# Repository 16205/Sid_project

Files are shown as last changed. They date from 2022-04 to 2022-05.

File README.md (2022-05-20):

# **SID Project**

#### A Robotic project - Stereo Imaging Device  
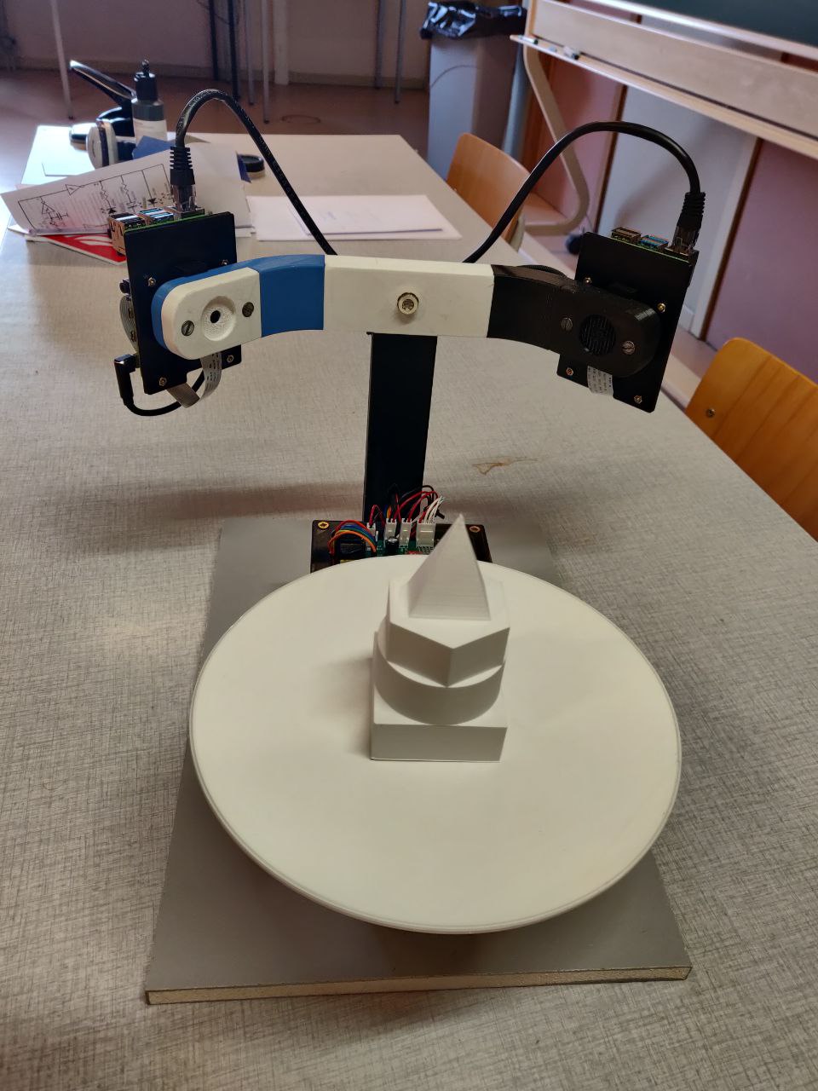
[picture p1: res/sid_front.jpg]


## Project participants  

- Nicolas SAMELSON 17288
- Raphaël JADIN 21295
- Gabriel LOHEST 16205

## Introduction

The goal of this project was to design a 3D scanner, develop an interface and scripts to output the scanned object into a 3D STL file, ready to import into a 3D CAD design software.  

This project is still in a phase of a prototype and therefore not a finnished product.  
All the files for the interface, the script, the PCB and the 3D CAD designs were developped in an "Open-Box" extensibility model. The ```main``` branch contains the code, the ```pcb``` branch contains the PCB design files and the ```3D-printed-hardware-CAD``` branch contains the models to print.  

## 1. Material used

- 2 Raspberry pi 4
- 2 Raspberry pi camera (module V2.1)
- 1 Stepper motor (Nema 17 10:1)
- 1 driver (A4988)
- 1 Power supply AC/DC 5V and 12V
- 1 display 11"
- 1 red line laser (HLM1230)

## 2. Interface (Kivy)

The interface files are stored inside the folder [/code/screen/](https://github.com/16205/Sid_project/tree/main/code/screens). 
Inside, there are 4 files, each for a specific screen interface.  

### 2.1. HomePageScreen
This corresponds to the home page of the interface. The user is presented with 4 buttons : 
- **Run**, to access the ```RunScreen```;
- **Settings**, to access the ```SettingsScreen```;
- **Storage**, to access the ```StorageScreen```;
- **Exit**, to exit the application.

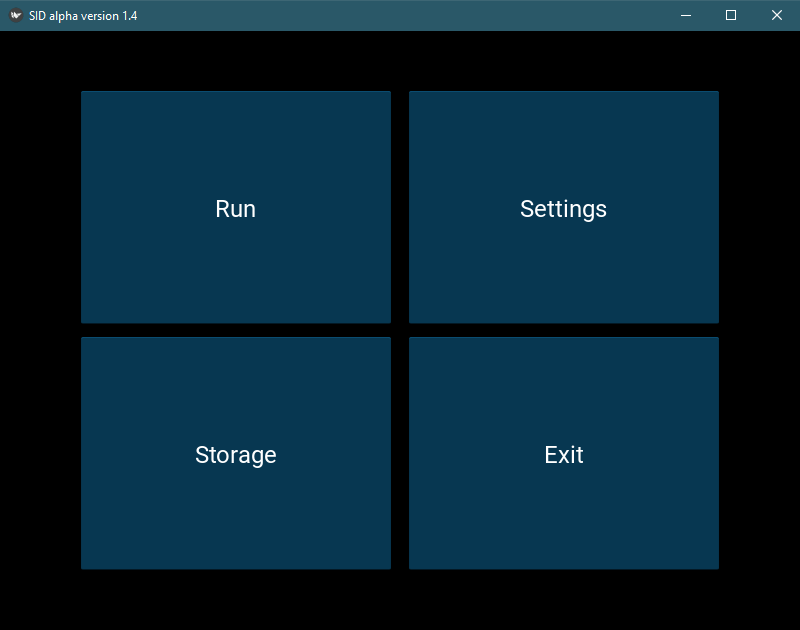
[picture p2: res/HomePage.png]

### 2.2. RunScreen
This interface contains all the quick parameters to set before a scan and the button to start a scan :
- **Resolution** is used to set the number of pictures taken;
- **Scale** is used to set the size of the object to scan;
- **Laser power** is used to adjust the intensity of the laser;
- **The set of 3 radio buttons** helps visualize the pictures taken in different color spaces.

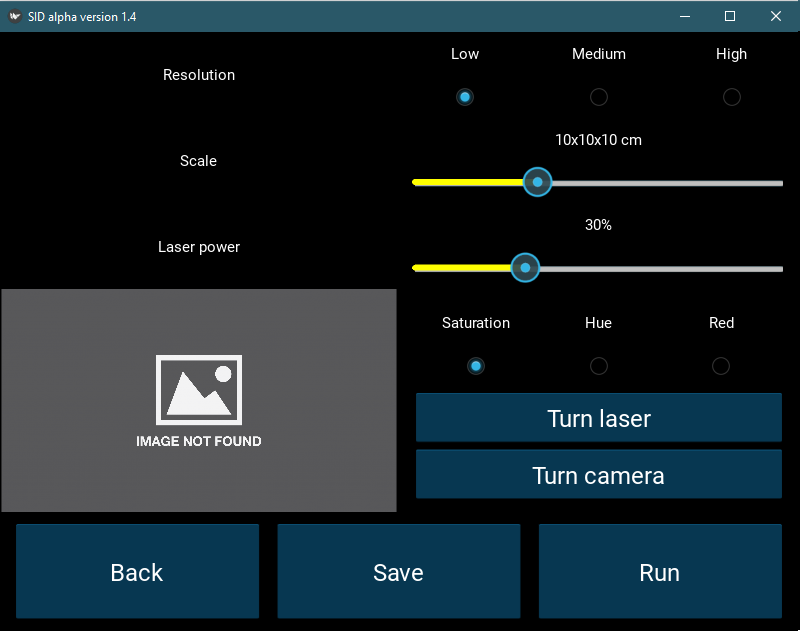
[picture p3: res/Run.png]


### 2.3. Settings
This interface is used to setup the calibration needed to scan (only the first time the application is launched) :
- **Connect** helps setting up the video stream of the slave raspberry pi camera;
- **Slave(L)** and **Master(R)** are used to have a video feedback of the 2 cameras;
- **Capture/Calibrate** launches the script of ```calibration```.

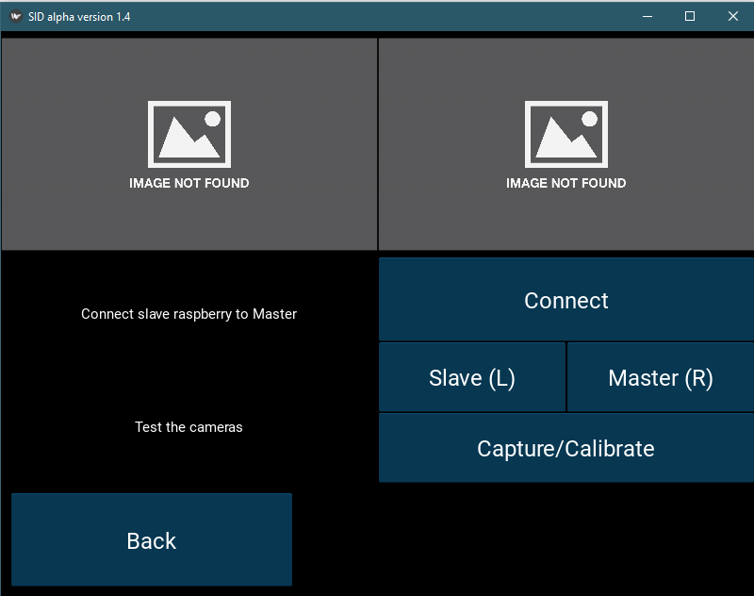
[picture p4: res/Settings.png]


### 2.4. Storage
The storage interface helps the user to manage its scans, as well as convert it in a 3D STL file.

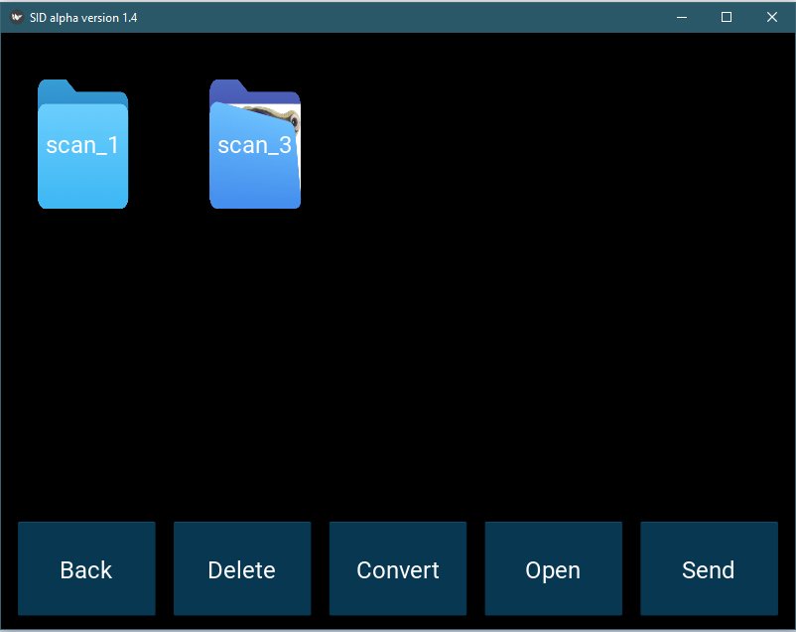
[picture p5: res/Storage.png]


## 3. Scripts

### 3.1. Main.py

Run the script [main.py](https://github.com/16205/Sid_project/blob/main/code/main.py) to launch the interface

### 3.2. On the Raspberry pi Master

#### 3.2.1. Different Files
In the [/code/raspberry/](https://github.com/16205/Sid_project/tree/main/code/raspberry) folder, you can find the following scripts :
- ```GPIO_setup.py``` : used to set the correct pins in read/write at the start of the application;
- ```copy_slave_pics.py``` : after a scan , the master will copy the pictures taken by the slave in its own folder;
- ```laser.py``` : used to turn on/off and adjust the intensity of the laser;
- ```prise_image_bon.py``` : takes a picture from the master and writes it into a folder with the name of the scan;
- ```scan.py``` : main script that manages the scan (turns the laser, takes pictures, turn the stepper and copy the slave pics);
- ```sshTools.py``` : used to run commands from the master to the slave via the SSH protocol;
- ```stepper.py``` : used to command the stepper and turn a determinated number of steps;
- ```stream.py``` : used to command the slave to stream its video feed through rtsp.

#### 3.2.2. Stereovision Folder
The stereovision folder contains the scripts to calibrate the cameras, but also to transform the pictures in a cloud of 3D points : 
- ```calibration.py```: calibrates the cameras;
- ```prepross.py```: generate a new binarized image with in white the laser and the rest in black
- ```image_processing.py```: contain the stereovision methods 
- ```scan_processing.py```: run the stereovision methods on a scan and then generate a JSON file with the world coordinates in the opencv calibration referential.
- ```post_processing.py```: achieve the revolution of all the laser lines and save the point cloud to a json.
- ```jsonTools.py```: Library to create json files and get data from json files
- ```mathTools.ty```: Library with mathematical functions for the image processing

#### 3.2.3. Post-processing Folder
This folder contains the scritps to transform a cloud of points into a 3D STL file : 
- ```create_stl.py``` : takes in input a json file in a 3 dimensions matrix and outputs a STL file;
- ```create_points.py``` : creates json files to get examples of working models.

### 3.3. On the Raspberry pi Slave
- ```prise_image_bon.py```: take picture and save it into the asked folder. Runned from the master in ssh.

## 4. PCB design
The [pcb](https://github.com/16205/Sid_project/tree/pcb) branch contains the Gerber files to print through JLCPCB.  
You can find the scematics and the design in the [pdf](https://github.com/16205/Sid_project/tree/pcb/pdf) folder.

The point of this PCB is to have one board, connecting all the needed cables as well as having easy access to the pins. It contains a footprint for :
- A A4988 driver;
- 2 USB-A 2.0 female ports;
- 1 capacitor (12V)
- 1 potentiometer
- pins for the stepper, the alimentation (5 and 12V), the laser and the raspberry pi (master)

## 5. Continue the project

Please Fork the repository if you want to continue our project. If you just want to test it, just clone it.

### 5.1. Dependencies

The project needs you to have a python version of ```3.8.10``` or older, with the following pip modules installed : 
- ```numpy```
- ```numpy-stl```
- ```opencv-python```
- ```mathutils```
- ```kivy```
- ```RpiMotorlib```

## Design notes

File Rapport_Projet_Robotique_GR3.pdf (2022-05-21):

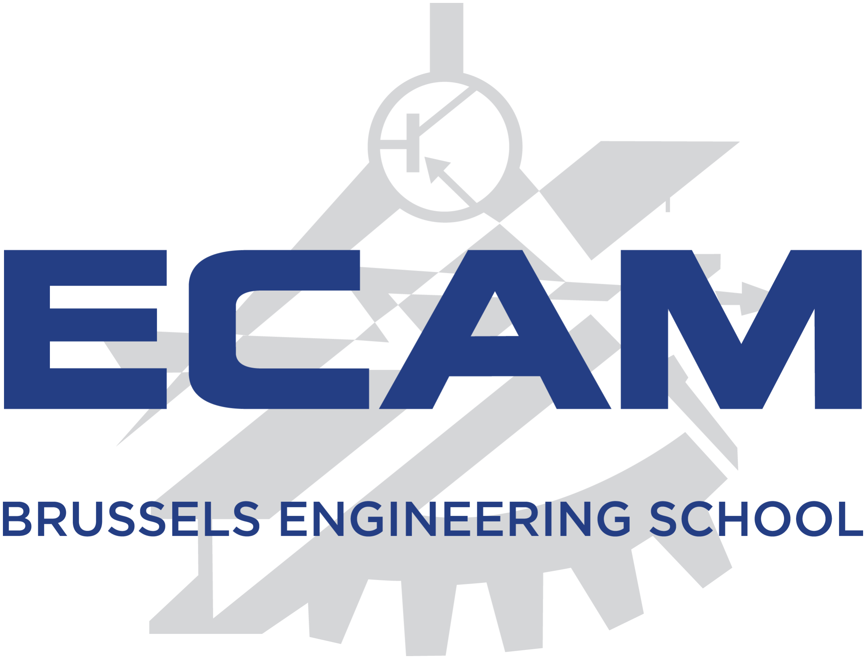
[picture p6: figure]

ECAM Brussels Engineering School

2021-2022

# Robotic Project:

## Stereo Imaging Device

Rapha¨el | JADIN | 21295
Gabriel | LOHEST | 16205
Nicolas | SAMELSON | 17288

May 21, 2022

## Contents

1 Introduction | 1
2 Materials and technologies | 2
2.2.3 | Image pre-processing, stereovision and point cloud post-processing . | 8
3 Project timeline | 13
4 Demonstration | 15
5 Critics & alternatives | 16
6 Conclusion | 20
References | 23

## List of Figures

1 | PCB design | | 2
2 | PCB schematic | | 4
3 | Slide rail mounting system separate design & testing | | 5
4 | Camera & laser housing, with Raspberry Pi supports | | 5
5 | Motor mount & rotating table | | 6
6 | Power supply case & vertical linking element | | 6
7 | Final assembly | | 7
8 | Image taken from the slave (Left) and image taken from the master (Right) | 9
9 | Generated binary pictures | | | 9
10 | Epipolar geometry | | 10
11 | Example of mesh | | 11
12 | Top view of a cylinder | | 12
13 | SID photo | | 15
14 | 3D mesh of the scanned piece | | 15
15 | Schema of the application with one laser and one camera | | 19

## 1 Introduction

The first 3D laser scanning device was developed in the 1960s, and consisted of lights, cameras and projectors. Due to the limitations of the equipment at that period, the scans took a lot of time and effort to be roughly accurate. It’s only in the end of the 20th century, with the democratisation of computers that the technology took a big leap forward. The methodology carried on improving, by making a scan more accurate, faster, truly three dimensional, and able to distinguish surfaces by color.
Later, with the democratization of 3D printing devices in 2005, the 3D laser scanning market grew even further.

During the Robotic Project course, we focused on creating a 3D scanner device, with the technologies of a laser and 2 cameras. Our objective was to make it open-source, affordable and modular, allowing a large range of compatibility with components.

The scanner is able to scan objects of a maximum size of 14cm in diameter and 15cm in height. The object is placed on a rotating plate, which is controlled by one of the two Raspberry Pi 4. After a scan, the device will transform the images taken in a 3D point cloud through stereovision technology. Finally, the user will be able to export a 3D file (in STL format) which could be imported into a 3D CAD software.

1

## 2 Materials and technologies

### 2.1 Hardware

Below is a list of the components used in this project. As mentioned earlier, the project is open-source and the design is modular. This means that the components could easily replaced by other ones.

List of components :

- 1x 11-inch LCD touchscreen
- 2x Raspberry Pi 4
- 1x 5 mW stripe laser
- 2x Pi Camera v2
- 1x NEMA 17HS15 stepper motor
- 1x A4988 Driver
- 1x AC/DC 5V and 12V power supply
- 1x Custom designed PCB
- 1x Custom 3D-printed assembly
- 2x USB-A to USB-C cables
- Multiple breadboard jumper wires

### 2.1.1 PCB & wiring

A PCB has been designed to handle all connections between the 2 Raspberry Pis, the stepper motor, the laser and the power supply. It was sketched with the help of the software EasyEDA.

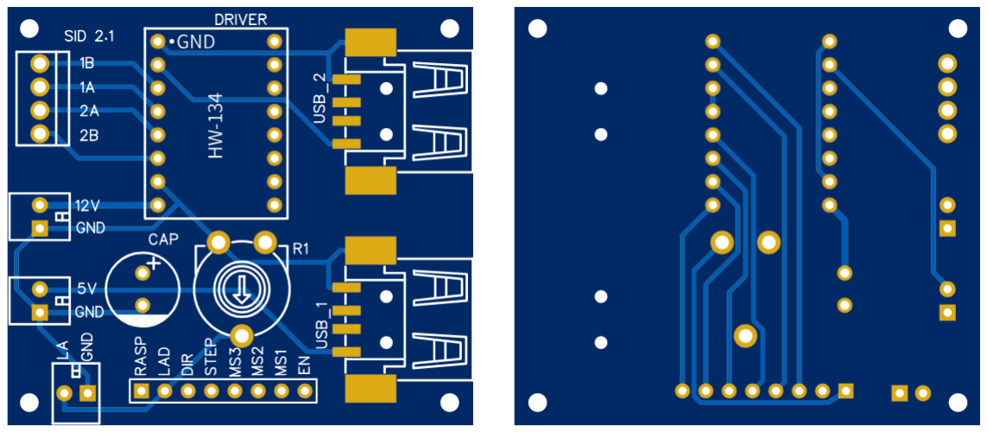
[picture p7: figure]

Figure 1: PCB design

2

On the PCB design at Figure 1, we can find footprints for the A4988 driver, 2 female USB-A ports, a potentiometer, a capacitor, and 5 blocks of connectors :

- 2x 2-pin connectors, used to connect the power supply outputs (5V and 12V)
- 1x 4-pin connector, to plug in the stepper motor
- 1x 2-pin connector, to plug in the laser
- 1x 8-pin connector, to link the Raspberry Pi and control the components.

First, the power supply brings 12V and 5V on the PCB. The 12V is used to power the stepper motor, which accepts a voltage between 9V and 35V. The 12V tracks, which are 0.69mm thick, pass through the driver. A 100 µF capacitor is also connected in parallel to the 12V source (see Figure 2).
The 5V tracks, which are 0.49mm thick, power the driver itself as well as the rest of the components.

The 2 USB ports are used to power each Raspberry Pi through a USB-A to USB-C cable. On the schematic (Figure 2), the USB connectors we used have the GND and VCC pins inverted (the component in red) between the schematic and the actual footprint, and therefore precaution is needed to avoid a short-circuit.

The 8-pin connector is used to control all components with the Raspberry Pi.
The 2 first pins (RASP and LAD) are used to power the laser. LAD connects it directly to the laser connector while RASP is connected in series with a potentiometer. This was originally intended to help the user control the intensity of the laser (with a knob on the potentiometer) in case the control through software wouldn’t be reliable (the Raspberry Pi needs to use its Pulse Width Modulation).

The 6 other pins are used to control the stepper motor. The DIR and STEP pins are used to control the direction of the rotation and the instruction to make a step, while MS1, MS2 and MS3 determine what the step size should be (the Nema 17HS15 is able to go down to a 16th of a step thanks to its gearbox [ref. 24].
Finally, the EN pin enables or disables the stepper.

3

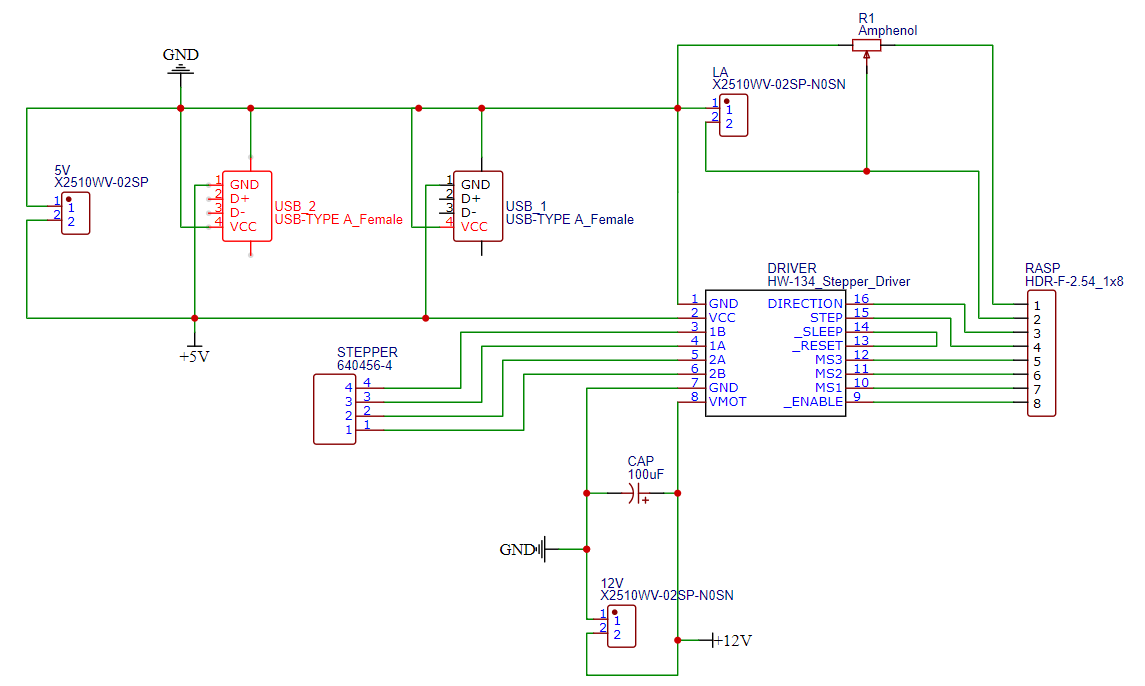
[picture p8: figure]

Figure 2: PCB schematic

4

2.1.2 3D Design & printing

The main body of the project is made of several 3D-printed parts, that have all been designed with Dassault Systemes’s SOLIDWORKS software. The initial goal was to be able to integrate all components in a single piece of hardware, so that the project could hold itself together as a whole. This has been achieved, thanks to a modular approach, resulting in a number of individual parts.

A slide rail mounting system has been conceived and separately tested before being integrated to most parts. This solution was chosen in order to make it easier to iterate design changes, to avoid having to print out the whole thing again at every new version. It also happened to be convenient because the 3D printer had a limited footprint. The slide rail mount also eliminated the need for fasteners, like screws and bolts, or even glue, thus making the final assembly an easier process.

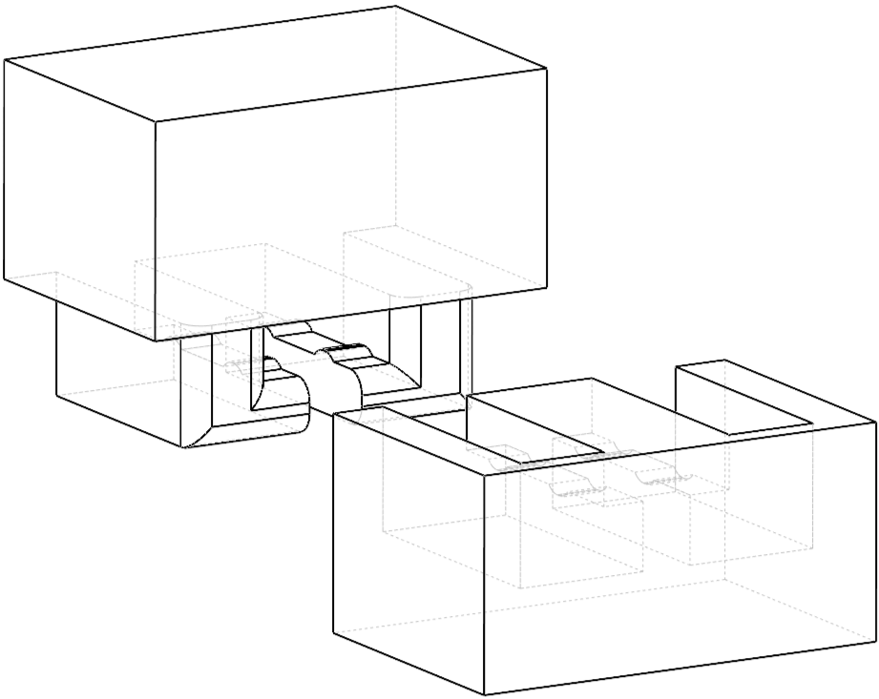
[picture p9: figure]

Figure 3: Slide rail mounting system separate design & testing

The assembly is essentially composed of 3 main parts, which are themselves made of subparts. The camera and laser housings, with the supports holding the raspberries in place. This is a nearly symmetrical part, except for a few details.

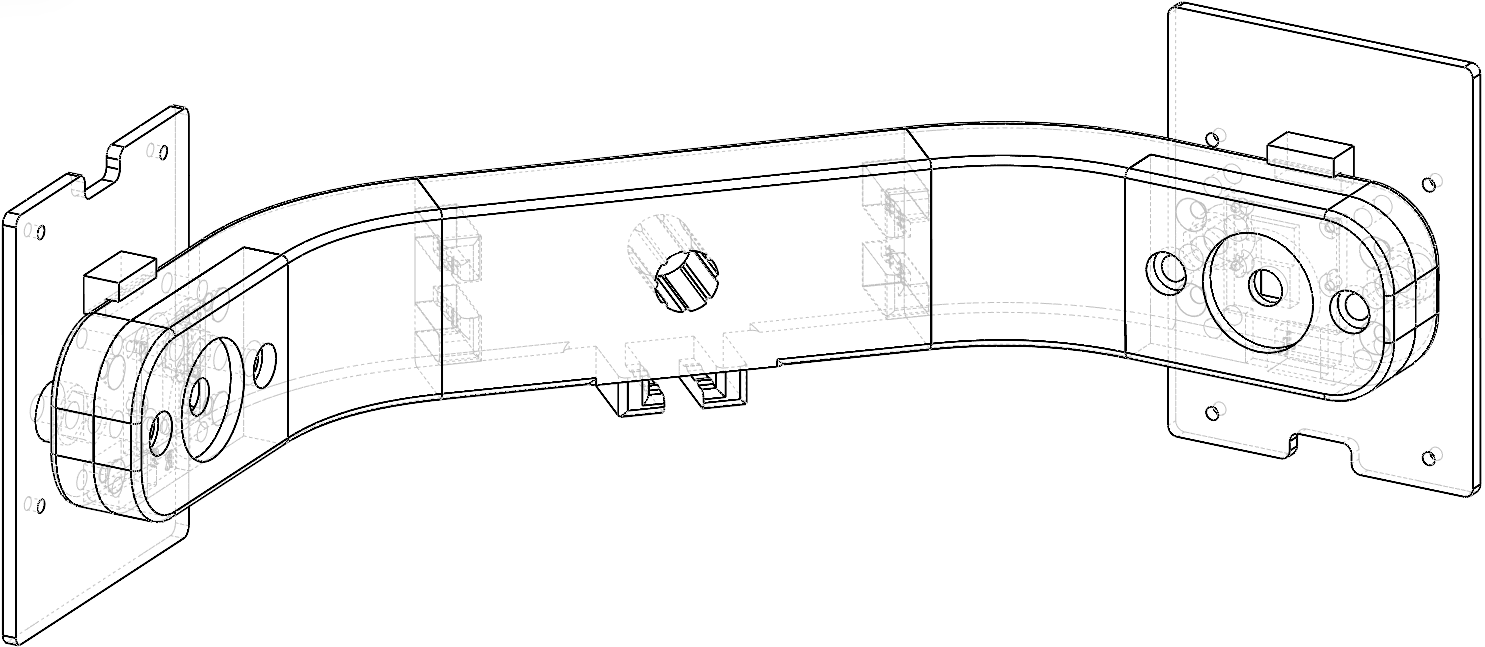
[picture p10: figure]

Figure 4: Camera & laser housing, with Raspberry Pi supports

5

Then, we have a motor mount for the Nema stepper motor, and a rotating table, lying on an appropriate thrust roller bearing, serving as mechanical coupling between the two.

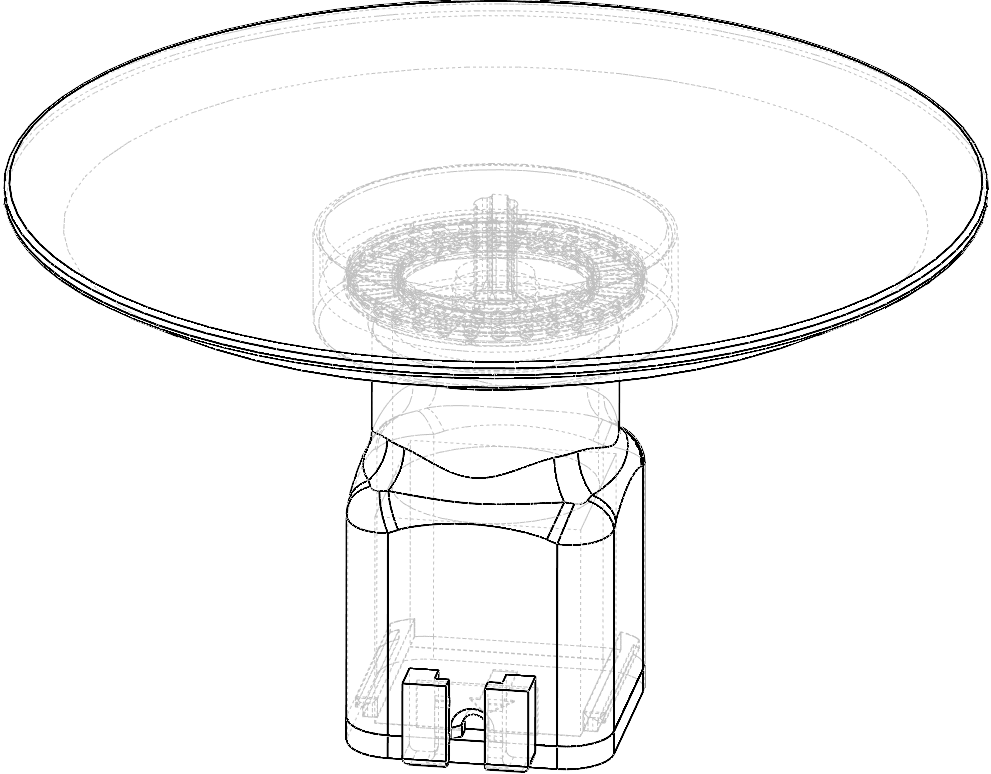
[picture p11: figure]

Figure 5: Motor mount & rotating table

Finally, the power supply case holds all the wires, the PCB, as well as the power supply unit. The vertical link part that connects to the camera and laser housing has a groove serving as a guide for the wires.

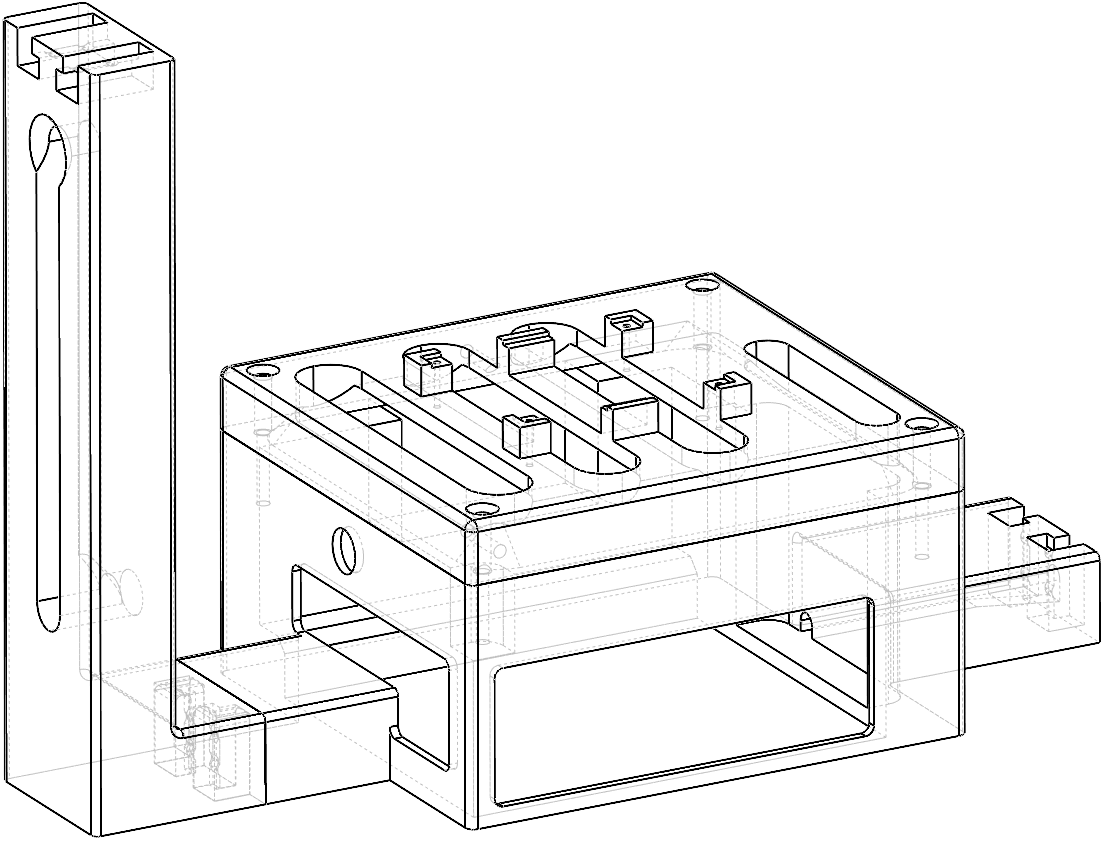
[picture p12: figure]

Figure 6: Power supply case & vertical linking element

6

The final assembly looks like this:

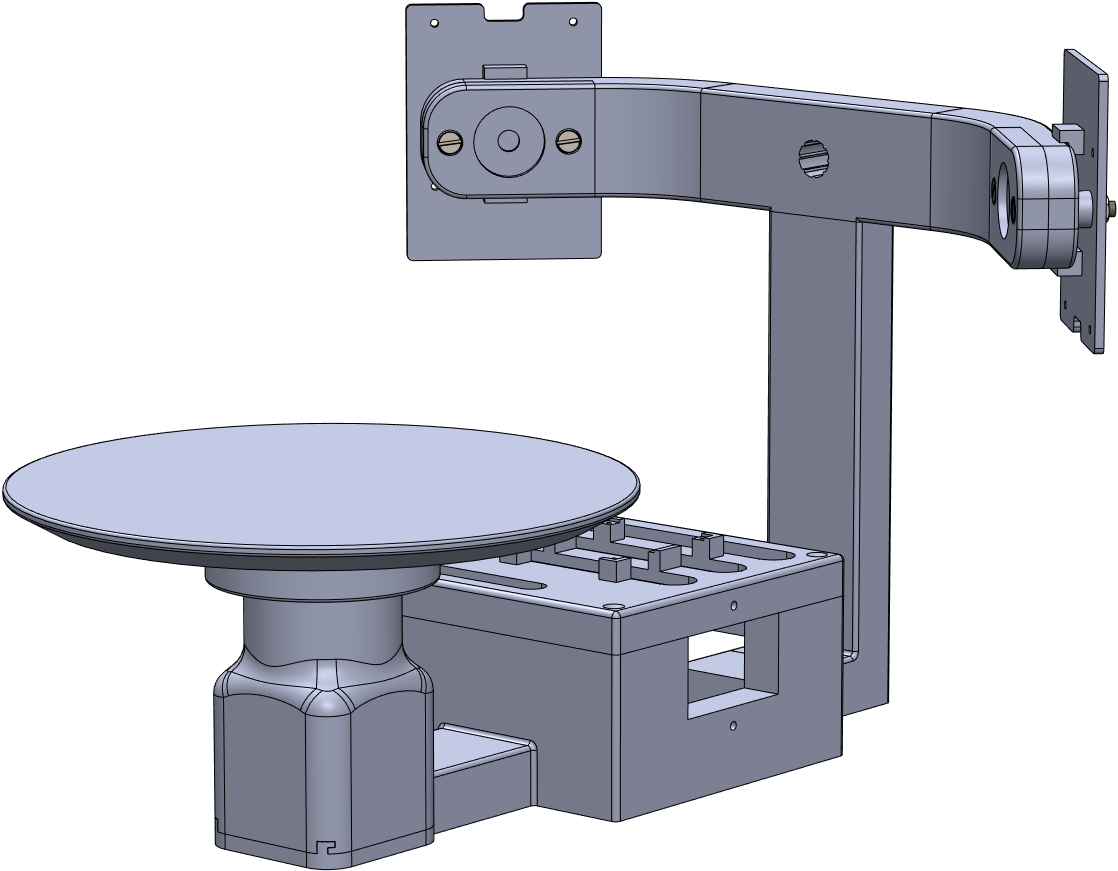
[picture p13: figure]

Figure 7: Final assembly

The choice was made not to integrate the touchscreen into the assembly. This is because of its bulky dimensions, but mainly because there were doubts during the development of the project as to whether it was needed or not. However, it ended up being part of the prototype, and can easily be connected and put in position right next to the project assembly, thanks to its integrated folding leg.
All files concerning the 3D CAD are available on GitHub [ref. 22].

### 2.2 Software

### 2.2.1 User Interface

For the user to be able to interact with the scanner, we have connected a 11-inch touchscreen to the Raspberry Pi master. In order to create the UI, we used the Kivy framework (based on python) as it offers cross-platform ability, an easy interaction and works well with touchscreens.

The UI is used to start the connection between the 2 Raspberry Pi’s together, calibrate the cameras, launch a scan, and convert the scan into a usable 3D file (STL format). A complete description of each page and their functionalities can be found on GitHub [ref. 21].

7

### 2.2.2 Communication protocols

Because we are using a second Raspberry pi (to connect the second camera), we used multiple communication protocols in order to take pictures on the slave and also to copy files from the slave to the master.

NFS

NFS, or Network File System, is a protocol that allows a client computer to mount a remote computer’s disk to its own file system, in order to access the remote files over the network. In our case, we implemented it to share the home folder of the slave Raspberry Pi over the master Pi. The network connection between both computers is secured by an Ethernet cable.
By accessing the files of the slave Pi via NFS, we can retrieve the images taken during the scan, and considerably faster than over another protocol, like for example, SSH.

SSH

The SSH protocol is widely used to remotely access the terminal of another machine. In our specific case, we used it to send commands to the slave Pi, for it to capture an image when needed.
The goal here is to run the script prise_image.py, which is stored on the slave Pi. This script, when run, triggers the capture of a picture with the slave Pi’s camera, and then stores that picture on the slave Pi’s own file system. One tricky part was to use SSH from a script on the master Pi, instead of directly from the terminal. In order to achieve this, we used the pexpect [ref. 18] and pxssh [ref. 20] libraries. Another difficulty arose, concerning the robustness; we need to make sure the slave Pi’s image has been captured, before the stepper makes the next step. To solve this problem, we used the NFS to check whether the image was successfully taken. If so, the stepper was then instructed to do the next step; if not, the image-taking script was re-run on the slave.

RTSP

RTSP, or Real-Time Streaming Protocol, is a network protocol designed to transport information streams, such as a video live-stream, over a transport protocol (i.e. UDP [ref. 31] or TCP [ref. 29] ).
In our case, it is used for the cameras’ calibration. The calibration script launches the stream on the slave, through SSH. The master is then able to access it and take video captures.

### 2.2.3 Image pre-processing, stereovision and point cloud post-processing

This part is composed of three main steps. First, we need to get the image coordinates (i.e. the x and y position relative to the upper left corner on the image) of the pixels which represent the laser projection. Then, based on those points, the stereovision technology is used to get the world coordinates of the points (i.e. the coordinates in a referential given by the OpenCV calibration). Finally, we need to process all the points in such a way that allows to model the scanned object.

8

Image pre-processing

This is the part where the images taken by the camera are processed in order to isolate the geometry of the laser projection on the object. A binary image¹
is then generated:
the pixels are black everywhere, except where the laser projection was detected, where the pixels are white.
To this purpose, the OpenCV library was used. This is an open source library developed by Intel, dedicated to image processing. It can be used in C++ or in Python, the latter of which is our case.

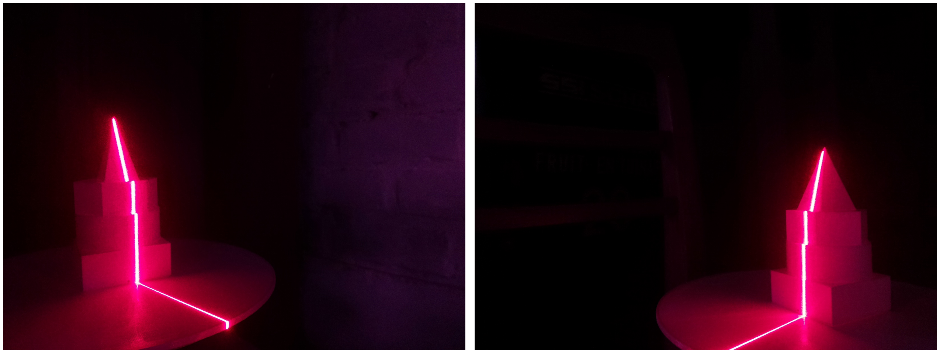
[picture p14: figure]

Figure 8: Image taken from the slave (Left) and image taken from the master (Right)

On the images at Figure 8, one can observe that the center of the laser line appears to be white. This is due to the intensity of the laser, that saturates the sensors of the cameras. In order to isolate the desired pixels, we took advantage of this. The threshold function of OpenCV was used on all three channels of the image (blue, green and red). This allows to generate these binary images, containing the laser line.

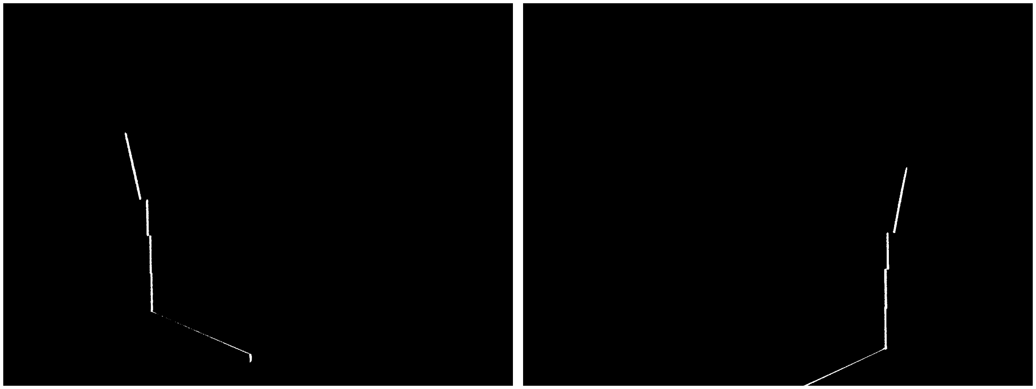
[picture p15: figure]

Figure 9: Generated binary pictures

Thanks to these cleaned up images, the actual stereovision processing can now start!

1A binary image is an image where the pixels have two possibles values: 0 for black and 255 for white

9

Stereovision

The following explanation is about one single left and right image pair at a time, but the process is obviously looped in such a way that all image pairs of a scan are processed in this way.
The first step is to narrow the laser line’s width down to a single pixel, on the binary image from the left camera, by taking the average coordinates of that width. These coordinates are then stored in the following format: (x = average x, y = line number, z = 1).

The next step is to find the corresponding pixels on the binary image from the right camera. This is done thanks to the epipolar geometry [ref. 7].

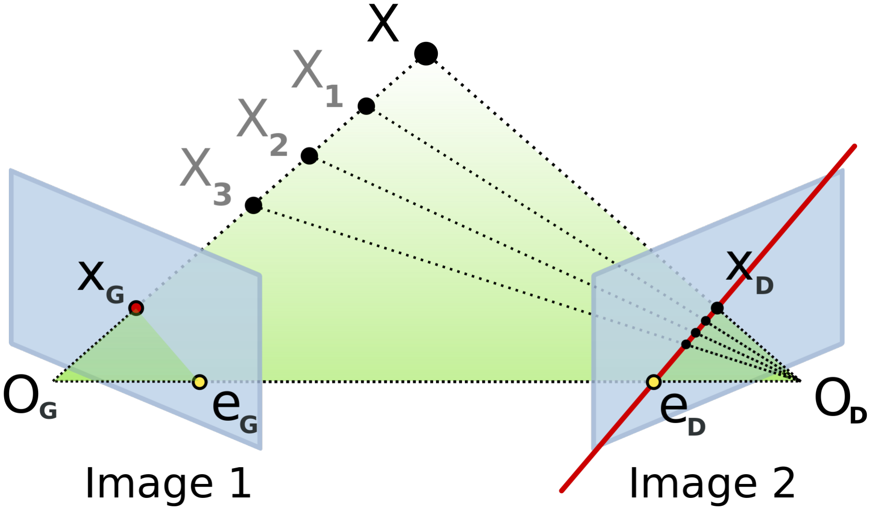
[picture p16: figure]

Figure 10: Epipolar geometry

Then, matching the pixels from the left and right images (i.e. XG on the left image and XD on the right image, in Figure 10) makes it possible to find the intersection of the [Og, XG] and [OD, XD] lines, on Figure 10. The coordinates of that intersection are in fact the previously mentioned ”world coordinates” of the laser line.
As every pair of left and right images corresponds to a step of the motor, all the world coordinates from a pair of images are stored in a JSON file, and referenced as follows :

{stepn : [[Y1, Y1, Z1, 1], [X2, Y2, Z2, 1], ..., [Xp, Yp, Zp, 1]], stepn+1 : ...}

each point having coordinates in the homogeneous [x, y, z, 1] form.

At this point, the current coordinates do not yet permit the reconstitution of the scanned part. To make this possible, we need to integrate the concept of rotation in order to stitch together all the data from every individual image pair, to be able to create the point cloud model. This is done in four steps :

1. Apply a transformation to move the origin of the coordinate system given by the OpenCV calibration (”world coordinates”), to the center of the table of the scanner.
2. For each step of the motor, and thus each image pair, a rotation has to be applied. The rotation angle for each image pair, or step n, can be computed as follows:

α = step angle ∗ stepn

where step angle is the angle covered by a step.

10

3. Find the ratio between a distance unit in the virtual referential and a millimeter in the real world.
4. Convert the homogeneous coordinates to ”real-world coordinates” in a referential with the same origin but where a unit is one millimeter.

Once all these steps are done, every ”real-world point” has to be written in a JSON file in the same way than previously explained. This JSON file then contains what we call the point cloud model of the object. The coordinates are organized in such a way that every column is the set of points from a step, i.e. a pair of pictures. This formatting is well suited for the point cloud post-processing.

### 2.2.4 Point cloud post-processing

The script create_stl.py takes care of the transformation of the point cloud into an exploitable STL file. When run, the script first retrieves the point cloud JSON file, and transforms it in a 3-dimensional array of points. The first dimension is the column (each column representing a step in our scan), the second is the row (or the points) and the last dimension contains the x, y and z coordinates of each point.

[
[[1.0, 0.0, 0], [1.0, 0.0, 1], [1.0, 0.0, 2]],
[[-1.0, 0, 0], | [-1.0, 0, 1], | [-1.0, 0, 2]]
]

In the example above, we have a 3D array of 2 columns and 3 points for each column. The 3D array is constructed with the help of the numpy library, allowing fast manipulations of arrays.

Before turning the 3D array into a STL file, each column of the point cloud needs to have the exact same amount of rows (or points). This is because a 3D mesh is constructed of triangles (see Figure 11). In our case, 2 triangles are formed from 2 points of 2 consecutive columns. For example on Figure 11, the triangle a and b are based on four points (2 are in common).

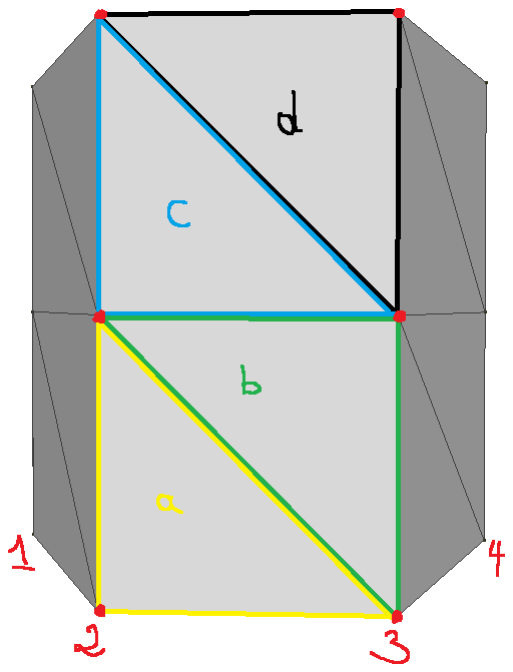
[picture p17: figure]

Figure 11: Example of mesh

11

In order for all columns to have the same amount of points, the array has to be processed by an algorithm that adds missing points where it is needed. We set the reference column as the one with the biggest number of points in it, in order to keep maximum resolution.

This algorithm first checks the endpoints of each column and compares it with its neighboring columns (e.g. we study the column number 2 on Figure 11, its neighbors are the column 1 and 3). As the first item in the column is the point with the lowest z coordinate and the last the highest z coordinate, we can compare those heights with with the endpoints of the neighbors columns. If the difference in height between the studied endpoints (bottom and top of column 2) and its neighbor endpoints (column 1 and 3) are greater than 10%, it fills in a new point at the mean height of its 2 neighbors.

The second part of the algorithm adds missing points between the 2 ends. This is done by calculating the average step the studied column should have, with the following formula :

step = lowest +

highest − lowest + 1
max rows
where
- lowest is the first item of the column, which has the lowest z coordinate,
- highest is the last item of the column, having the highest z coordinate,
- max rows corresponds to the number of points the reference column has.

For a given step, we can iterate through its column and add missing points if the difference between the step and the next point’s z coordinate is greater than 10%. After repeating this for each column of the array, they should now all have the same number of points.

We can now transform the 3D array into a 2D array of vertices and faces. The vertices correspond to our points in the 3D array that is flattened into a 2D array [ref. 15].
The faces are an array of the triangles we construct. A single triangle needs 3 points, and for the mesh to show the face in the correct direction, we need to order the 3 points as to draw it clock-wise (if we were to join the 3 points together).

Now all the points (vertices) are linked to triangles. But the top and bottom of the object are still not connected. To solve this problem, we can simply add a point in the middle at the top of the piece (see Figure 12) and draw triangles between the center and 2 points at the top of their respective column. The same was done for the bottom.
Finally, with the help of the numpy-STL library, we can create a 3D mesh and save it in STL format.

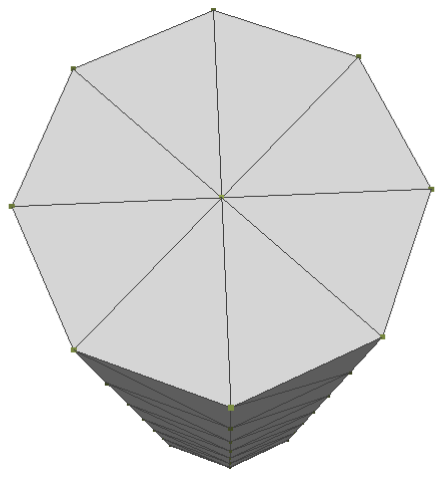
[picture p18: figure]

Figure 12: Top view of a cylinder

12

## 3 Project timeline

### 3.1 Sprint 1

- design a PCB for the driver;
- first version of 3D design for laser and camera support;
- establish the connection between the slave Pi and the master Pi;
- validate and command the pcb;
- taking images from both rapsberry pi and transfert the images from slave Pi to master Pi;

### 3.2 Sprint 2

- first verion of the U.I.;
- design the box for the stepper motor and the scanner’s table;
- print the box for the stepper motor;
- calibrate the cameras;
- import the U.I. on the master PI;
- test and weld the components on the pcb;
- finalize the U.I.;

### 3.3 Sprint 3

- make the stepper operational;
- insert the code of the stepper into the U.I.;
- 3D design : attached the slide rail;
- insert the scripts for the scan in the U.I.;
- finalize the pcb and the wiring;
- new supports for the camera and the stepper motor.

### 3.4 Sprint 4

- achieve a scan of an object and get pictures from the slave;
- extract the pixels of the laser and get their world coordinates;
- make a json with the coordinates of the extracted points from the scan and format it properly;
- all the 3D pieces are printed and fits together;

13

- image processing code refactored to make it more extensible;
- create an stl file from a point cloud
- cable management is done properly;
- camera calibration is runable from the interface.

14

## 4 Demonstration

A piece was placed on the center of the table (see Figure 13). We launched a scan which took a 100 photos (for each camera). Here is the result of the 3D mesh in a STL format at Figure 14.

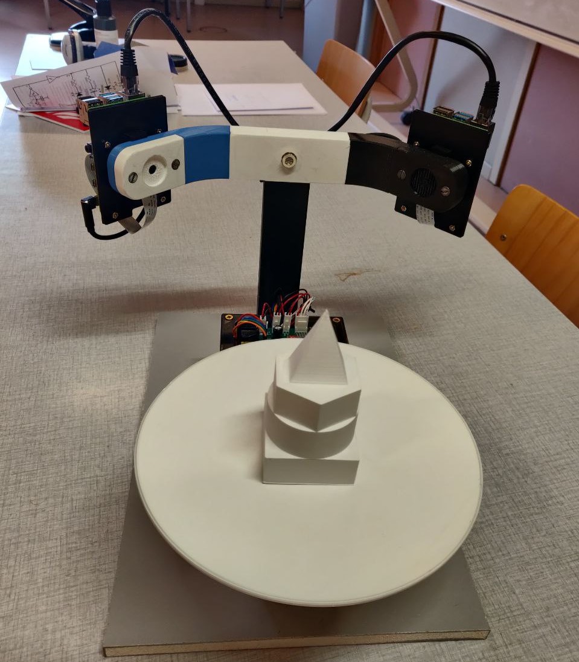
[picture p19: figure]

Figure 13: SID photo

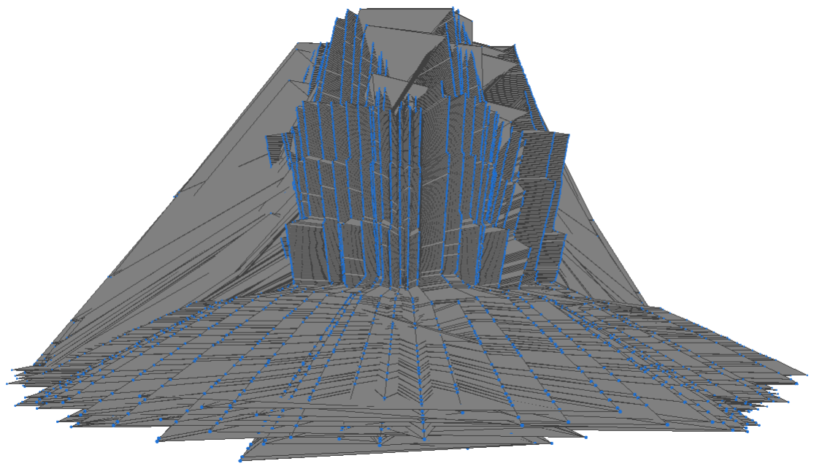
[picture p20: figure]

Figure 14: 3D mesh of the scanned piece

One can see that the table has not been removed from the model.

15

## 5 Critics & alternatives

### 5.1 Initial specifications retrospective

The goal of this project was to produce a device able to precisely scan an object of small size (14cm in diameter, and 15cm in height) thanks to its cameras, and output a usable 3D file. The objective has been partially met. The device is indeed able to scan an object and output a 3D file, (Figure 14) but due to poor calibration, the accuracy and precision of the scan is not in par with the expectations, even if every part is working properly.

### 5.2 Difficulties encountered

During this project, we faced many difficulties that we tried to resolve, some of which couldn’t be overcome, so we could not fulfill some of the specifications we presented during Q1 of this year.

Kivy framework

First, on the software side, we encountered many difficulties with the Kivy framework. One of them was that the framework is a single threaded application. So, when we run a scan, the whole app is blocked, waiting for the script to end. Due to the limited time, we have not been able to explore and implement multi-threading on Python.
Also, for an unknown reason, Kivy was handling 2 video feeds and the implementation of OpenCV’s video capture very badly.

Communication between the Raspberry Pis for image capture

Other protocols than the ones used (SSH) were studied, to try to improve the latency, quality and time between each scan, but the latency remained roughly the same as the RTSP (over 8 seconds and very inconsistent). So, we decided to run SSH commands in a loop, which gave more control of the moment of the image is captured. We concluded that the main limitation was the Kivy framework as outside of the app it could run more smoothly. And as we couldn’t get a confirmation that the 2 video feeds had the same latency, we kept using the SSH protocol.

Calibration

In order to use the epipolar geometry, we need several parameters about the system, like the cameras’ optical center coordinates, their projections matrices and the fundamental matrix of the system. This is done thanks to the calibration function of OpenCV. The problem is that this function takes quite a lot of time to master. Hence, since this wasn’t the only time consuming task, it turns out we did not have enough time to do it properly so our calibration isn’t totally correct. This results in some error in our model of the scanned object. This error can easily be removed with a better calibration. One part of the problem here was that in order to get a good calibration, we need the (very) precise physical location (relative to the rotating table) of the bottom left corner of the chessboard that is put in place when proceeding to make the calibration. This is further discussed in the subsection 5.3.

16

Optimisation of the computations

Since the Raspberry Pi has limited RAM, we needed to optimize our computations in order to avoid memory saturation. For the image processing and the stereovision, we kept this in mind at all times when developing, due to the amount of data to be processed. Special care was also put into the robustness and the extensibility of the code.

Point cloud post-processing

The algorithm responsible for turning the point cloud into a 3D mesh was coded from scratch, and as we were limited in time, it is quite basic compared to other existing algorithms. Furthermore, it is handling the points in a somewhat naive way, and does not remove any aberrant point (with absurd coordinates). This is one of the reasons why the final result is not very conclusive.

### 5.3 Improvements

With the many issues we encountered during development, we thought about multiple improvements we could bring if we had more time to put into the project.

Communication protocols

First, we would dedicate more time into finding a reliable solution concerning communication protocols. Indeed, outside of the Kivy environment, our streaming tests over the TCP protocol were very concluding (less than a second of latency and very consistent). We would have liked to implement this, after finding a way to make sure the pictures were taken at the same time. This could potentially improve the speeds of the scanning process by factor of about 10, which would make a scan with the highest resolution (4000 steps) reasonably fast (∼ 2h, vs ∼ 20h currently).

Calibration

The calibration could be enhanced in different ways. A good way to improve it could be to dedicate a whole project to it, since the calibration is a quite demanding task by itself, both in terms of time and expertise. The goal of that project would be to automate the calibration with a homemade script, eliminating the need to manually measure the offset between the center of the calibration’s reference frame and the center of the rotating plate.

Image processing

One of the biggest improvements we could achieve concerning the image processing would be to remove the scanner’s table from the detected points. Indeed, if the scanned object is smaller than the table, part of the table is also going to be included in the model, which is unwanted.

17

Another reason to remove the table points while proceeding to the pre-processing, is that these points being useless, it makes sense not to process them, to avoid consuming resources unnecessarily.
A good way to achieve this would be to take an image with each camera of an empty table and the laser turned on. Then, by comparison between the empty table and the images of the scan, it should be possible to remove the undesired data from the scan.

Point cloud post-processing

As mentioned in the subsection 5.2, the algorithm is rather primitive, and cannot handle aberrant points. We would suggest to take more time in tweaking the algorithm, improving its robustness, smoothing surfaces, etc.
An alternative to this would be to use yet another python library (e.g. Open3D library [ref. 10]) , which handles all the algorithms necessary to build a 3D mesh.

Turntable
Another good idea would be to cover up the turntable with rubber, in an effort to increase the friction between the scanned object and the turntable. This can be useful to make sure the object doesn’t skid around every time the stepper motor makes a rotation impulse. This could also be helpful for the image processing responsible for removing the turntable from the scanned points.

### 5.4 Alternatives

As mentioned earlier, we had a lot of issues related to the communication protocols, as consequence of the design constraint of using 2 Raspberry Pis 4 (to be able to use a second camera, since a Raspberry Pi only has one single camera port).
In the specifications we presented on Q1 this year, we first wanted to use a single Raspberry Pi 4, along with a multi-camera adapter [ref. 11]) , making it possible for a single Pi to hande both cameras. There were also other alternatives, like using a Compute Module 4, webcams over USB, or even the Arducam synchronized stereo camera HAT. However, due to the chip shortage during 2021, most of those components were out of stock until later in 2022.

If we had to start the project again from the beginning, we would definitely use one of the simpler single-Raspberry Pi alternatives mentioned above.

There are different ways to achieve a 3D scan with cameras. Another very promising method is the one with a single camera and a laser. This would of course require to precisely quantify the geometry (position, orientation) of the plane defined by the laser beam.

18

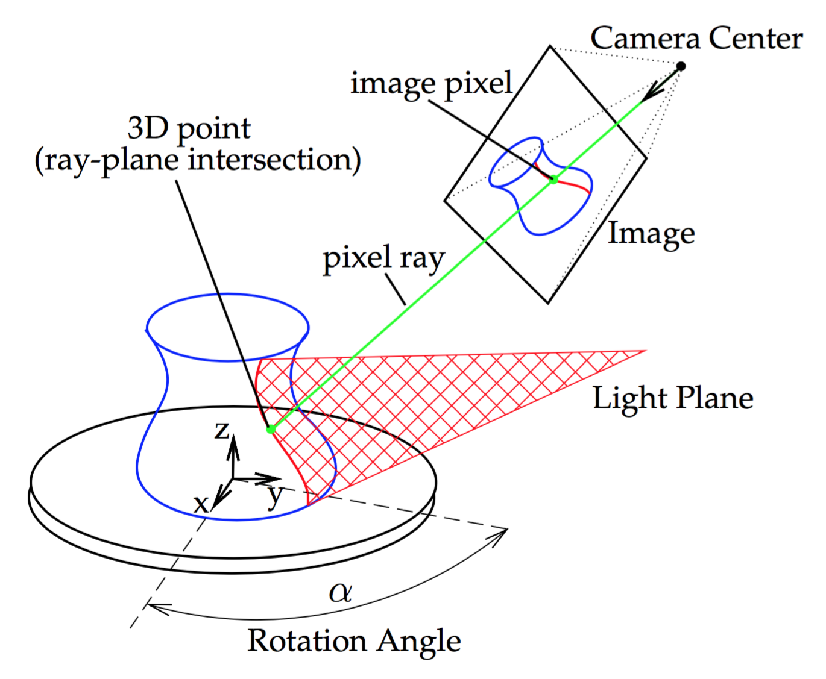
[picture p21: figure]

Figure 15: Schema of the application with one laser and one camera

Let’s define the line going through both the camera center and the image pixel, as the pixel ray, as displayed on Figure 15. By finding the intersection of that pixel ray with the laser light plane, one can easily construct the world coordinates of the point on the object (”3D point” on Figure 15). What follows is the same as our implementation, concerning what happens next with the world coordinates.

This method would drastically reduce the costs of our project, without negatively impacting its precision. Moreover, as there is a single camera, the overall complexity of the project would be far lesser, and way cheaper.

19

## 6 Conclusion

This project has been quite an enriching experience for us, as it allowed us to expand our knowledge and engineering skills. We have learned a lot in many domains.
First, the management aspect of a project taught us many things about the importance of planning and prioritizing tasks. Looking back on the overall organization, we regret not having followed the planning work accomplished on Q1, which was completely decoupled from the manner we actually proceeded. It is however safe to say that the division of labor between the partaking members was done quite right, considering each and every one’s strengths, even though some of us would have liked to get involved somewhat more in other tasks.

We also noticed that we took the biggest decisions when our knowledge of the subject was at its lowest. This has helped us understand the value of studying the subject before launching the project.

We have acquired technical skills that we would not have been able to develop in such depth during our school, career without participating in this kind of project. This is likely to serve us as a great asset in the future.

In closing, even though the end result is far from the original expectations, we managed to check all the specified tasks and release a functional prototype.

20

## References

[1] (PDF) 3D LASER SCANNERS: HISTORY, APPLICATIONS, AND FUTURE. url: https://www.researchgate.net/publication/267037683_3D_LASER_SCANNERS_HISTORY_APPLICATIONS_AND_FUTURE (https://www.researchgate.net/publication/267037683_3D_LASER_SCANNERS_HISTORY_APPLICATIONS_AND_FUTURE) (visited on 05/21/2022).
[2] 3D LASER SCANNERS: HISTORY AND APPLICATIONS. url: https://www.actasimulatio.eu/issues/2018/IV_2018_01_Edl_Mizerak_Trojan.pdf (visited on 05/21/2022).
[3] Aish Dubey. “Stereo vision—Facing the challengesand seeing the opportunities for ADAS applications”. In: (2020). url: https://www.ti.com/lit/wp/spry300a/spry300a.pdf (https://www.ti.com/lit/wp/spry300a/spry300a.pdf) (visited on 12/28/2021).
[4] Clayton Darwin. Distance (Angles+Triangulation) - OpenCV and Python3 Tutorial
- Targeting Part 5. 2018. url: https://www.youtube.com/watch?v=sW4CVI51jDY (visited on 12/26/2021).
[5] dtrewren. Ciclop 3D Scanner (BQ & Horus). Instructables. url: https : / / www . instructables.com/Ciclop-3D-Scanner-BQ-Horus/ (visited on 12/29/2021).
[6] Epipolar geometrie. url: https://upload.wikimedia.org/wikipedia/commons/9/9d/Epipolargeometrie-fr.svg (https://upload.wikimedia.org/wikipedia/commons/9/9d/Epipolargeometrie-fr.svg) (visited on 05/21/2022).
[7] Epipolar Geometry. url: https://www.cs.toronto.edu/~jepson/csc420/notes/epiPolarGeom.pdf (https://www.cs.toronto.edu/~jepson/csc420/notes/epiPolarGeom.pdf) (visited on 05/21/2022).
[8] FU-Fighters. “Stereo vision with a single camera”. In: (2004). url: http://www.inf.fu-berlin.de/lehre/SS06/Robotik/stereo_vision_newest.pdf (visited on 12/20/2021).
[9] Enric Meinhardt Gabriele Facciolo Carlo de Franchis. “MGM: A Significantly More Global Matching for Stereovision”. In: (2015). url: http://dev.ipol.im/~facciolo/mgm/mgm.pdf (http://dev.ipol.im/~facciolo/mgm/mgm.pdf) (visited on 12/29/2021).
[10] Generate 3D meshes from point clouds with Python — Towards Data Science. url: https://towardsdatascience.com/5- step- guide- to- generate- 3d- meshesfrom-point-clouds-with-python-36bad397d8ba (https://towardsdatascience.com/5-step-guide-to-generate-3d-meshes-from-point-clouds-with-python-36bad397d8ba) (visited on 05/21/2022).
[11] How to attach multiple cameras to Raspberry Pi - Arducam. url: https : / / www . arducam.com/docs/cameras-for-raspberry-pi/multi-camera-adapter-board/ introduction/ (https://www.arducam.com/docs/cameras-for-raspberry-pi/multi-camera-adapter-board/introduction/) (visited on 05/21/2022).
[12] Kivy: Cross-platform Python Framework for NUI Development. url: https://kivy.org/#home (https://kivy.org/#home) (visited on 05/21/2022).
[13] Machine-Vision-Applications. GeT Cameras, industrial vision cameras and lenses. url: https : / / www . get - cameras . com / Machine - Vision - Application (https://www.get-cameras.com/Machine-Vision-Application) (visited on 05/21/2022).
[14] Network File System - Wikipedia. url: https://en.wikipedia.org/wiki/Network_File_System (https://en.wikipedia.org/wiki/Network_File_System) (visited on 05/21/2022).
[15] numpy.ndarray.flatten — NumPy v1.22 Manual. url: https : / / numpy . org / doc / stable/reference/generated/numpy.ndarray.flatten.html (https://numpy.org/doc/stable/reference/generated/numpy.ndarray.flatten.html) (visited on 05/21/2022).
[16] OpenCV: Depth Map from Stereo Images. url: https://docs.opencv.org/4.x/dd/d53/tutorial_py_depthmap.html (https://docs.opencv.org/4.x/dd/d53/tutorial_py_depthmap.html) (visited on 12/29/2021).

21

[17] M. Pesce et al. “A Low-cost Multi Camera 3D Scanning System for Quality Measurement of Non-static Subjects”. In: Procedia CIRP. 3rd CIRP Global Web Conference
- Production Engineering Research 28 (Jan. 1, 2015), pp. 88–93. issn: 2212-8271. doi: 10.1016/j.procir.2015.04.015. (https://doi.org/10.1016/j.procir.2015.04.015) url: https://www.sciencedirect.com/science/article/pii/S2212827115002772 (https://www.sciencedirect.com/science/article/pii/S2212827115002772) (visited on 12/23/2021).
[18] Pexpect version 4.8 — Pexpect 4.8 documentation. url: https://pexpect.readthedocs.io/en/stable/ (https://pexpect.readthedocs.io/en/stable/) (visited on 05/21/2022).
[19] Pololu - A4988 Stepper Motor Driver Carrier. url: https : / / www . pololu . com / product/1182 (https://www.pololu.com/product/1182) (visited on 12/26/2021).
[20] pxssh - control an SSH session — Pexpect 4.8 documentation. url: https://pexpect.readthedocs.io/en/stable/api/pxssh.html (https://pexpect.readthedocs.io/en/stable/api/pxssh.html) (visited on 05/21/2022).
[21] Nicolas Samelson, Raphael Jadin, and Gabirel Lohest. 16205/Sid project: Projet Robotique - Scanneur SID. GitHub. url: https://github.com/16205/Sid_project/tree/main (https://github.com/16205/Sid_project/tree/main) (visited on 05/21/2022).
[22] Nicolas Samelson, Raphael Jadin, and Gabirel Lohest. 16205/Sid project: Projet Robotique - Scanneur SID - 3D CAD Branch. GitHub. url: https://github.com/16205/Sid_project/tree/3D-printed-hardware-CAD (https://github.com/16205/Sid_project/tree/3D-printed-hardware-CAD) (visited on 05/21/2022).
[23] Stephen Se and Piotr Jasiobedzki. “Stereo-vision based 3D modeling and localization for unmanned vehicles”. In: International Journal of Intelligent Control and Systems 13 (Mar. 18, 2008). url: https : / / www . researchgate . net / publication / 228618177_Stereo-vision_based_3D_modeling_and_localization_for_unmanned_ vehicles. (https://www.researchgate.net/publication/228618177_Stereo-vision_based_3D_modeling_and_localization_for_unmanned_vehicles)
[24] Stepper motor 17HS15. url: https://www.omc- stepperonline.com/download/ 17HS15-1684S-HG10.pdf (https://www.omc-stepperonline.com/download/17HS15-1684S-HG10.pdf) (visited on 05/21/2022).
[25] Super Make Something. DIY 3D Scanner (Arduino, 3D Printing, PCB Design, Stepper Motors, IR Sensing) - Super Make Something. Mar. 14, 2016. url: https://www.youtube.com/watch?v=-qeD2__yK4c (visited on 12/28/2021).
[26] The Coding Lib. Depth Estimation Using Stereo Vision - Computer Vision Project with OpenCV C++ Code. 2021. url: https : / / www . youtube . com / watch ? v = snJVyfl9ZMg (https://www.youtube.com/watch?v=snJVyfl9ZMg) (visited on 12/20/2021).
[27] The FabScan Project - Media Computing Group - RWTH Aachen University. url: https://hci.rwth-aachen.de/fabscan (visited on 12/29/2021).
[28] TI4L-L1 - Traitement d’images 1 (2021-2022) - General - All Documents. url: https: //bit.ly/3NqGWqF (visited on 05/21/2022).
[29] Transmission Control Protocol. In: Wikipedia. Page Version ID: 1088448616. May 18, 2022. url: https : / / en . wikipedia . org / w / index . php ? title = Transmission _ Control_Protocol&oldid=1088448616 (https://en.wikipedia.org/w/index.php?title=Transmission_Control_Protocol&oldid=1088448616) (visited on 05/21/2022).
[30] What is a stereo vision camera? — Camera blog. url: https://www.e-consystems. com / blog / camera / camera - board / what - is - a - stereo - vision - camera / amp/ (https://www.e-consystems.com/blog/camera/camera-board/what-is-a-stereo-vision-camera/amp/) (visited on 12/20/2021).
[31] What is User Datagram Protocol (UDP)? Definition from SearchNetworking. url: https : / / www . techtarget . com / searchnetworking / definition / UDP - User -Datagram-Protocol (https://www.techtarget.com/searchnetworking/definition/UDP-User-Datagram-Protocol) (visited on 05/21/2022).

22

[32] Zhiyi Zhang Zhihua Lv. “Build 3D Scanner System based on Binocular Stereo Vision”. In: (2012). url: https://cie.nwsuaf.edu.cn/docs/20170614173931092961.pdf (visited on 12/20/2021).

23

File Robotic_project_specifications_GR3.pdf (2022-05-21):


ECAM Brussels Engineering School

2021-2022

# Robotic project :

# Sid - 3D Scanner

Nicolas | SAMELSON 17288
Rapha¨el JADIN | 21295
Gabriel | LOHEST | 16205

### December 29, 2021

## Contents

1 Introduction | 1
2 Technologies | 1
3 Measurement logic | 6
4 Resolution and error on depth estimation | 8
5 Post-processing | 9
Bibliography | 13
Appendices | 14
A Raci Matrix | 14
B Gantt Diagram | 15
C Bill of Materials | 16

## 1 Introduction

The market of the 3D scanners being expensive, we focused ourselves on an opensource product that is affordable for end users. As the choice of the components, and their compatibility, is large, it will be possible to build with a tight budget, or aim for quality.

The scanner would be able to scan objects of maximum size of 10cm in diameter, and 20 cm in height.The device would then produce a 3D file, ready to be 3D printed or imported into any CAD software.
The scanner is equipped with a rotating plate, on which the object to be scanned is placed. The components used to scan are two cameras and a line laser. Two Raspberry Pi’s will be used to do all the processing.

## 2 Technologies

To scan an object, there are several technologies, so we initially narrowed it down to two of them :

- The LIDAR or Light Detection And Ranging ;
- The stereovision.

The LIDAR technology uses laser beams (which are safe for the human eye) to create a 3D representation of one’s surroundings. The LIDAR sends out a pulse of light and measures the time it takes for the light to return to the scanner, which enables it to calculate the surrounding depth information. It is widely used in the autonomous car industry, agriculture, biology and geology.

The principle of stereovision is the calculation of depth based on the disparity between 2 images of an object. The two images are taken at a different angle, and knowing the distance between the two cameras, we can calculate the distance of a point. For the case of a 3D scanner, we will not calculate a point, but a vertical slice of the object at a time. This slice can be highlighted with a laser.

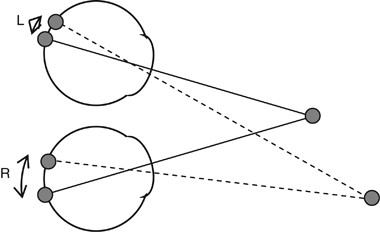
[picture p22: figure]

Figure 1: Principle of stereovision

1

It is also possible to use stereovision with a single camera, by placing two prisms in front of the camera, and 2 mirrors on either side.

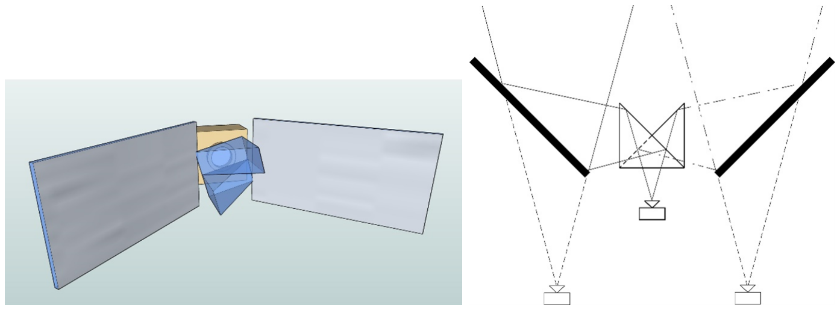
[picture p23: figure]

Figure 2: Stereovision with mirrors

### 2.1 Comparison and choice of the technologies

The LIDAR technology is the easiest to implement. In fact, it requires little math, and no calibration (unlike the stereovision method) to get distances. However, a sensor which can accurately detect objects within a range of less than one meter is difficult to find at an affordable price.

Therefore, we looked into stereovision technology.

For the cameras to maintain a high level of accuracy in dimly lit environments, we can use a laser. Moreover, it makes it easier to determine the region to be studied. In this regard, it is possible to use one or two cameras in several ways.

- One camera and two prisms and two mirrors;
- One camera and one laser;
- One camera and two lasers;
- Two cameras and one laser.

The first way is quite complex to set up, and makes it expensive to get a good image quality, due to the prisms and mirrors that come into play.

Then, it is possible to do it with a camera and a laser. However, this requires an additional stepper motor, in order to have two ”false” angles of view, thanks to the stepper that moves the laser on the object at a precise angle.

2

It is also possible to use a camera and 2 lasers instead of one laser and an additional stepper. This allows, compared to the previous solution, to be faster, because the 2 lines of lasers are found on each image. In addition, it has one less moving part, therefore it should be more accurate.

Finally, stereovision using two cameras and a laser is advantageous over a single camera and a laser, thanks to the speed and the quality of the scan. It is also easier to do the processing in order to recover the depths with two images than with one. However, the total amount of the project will be more expensive.

### 2.1.1 Choice of components

Component | Name | Advantages | Disadvantages | Price [euro]
Camera | Raspberry pi cam High res | 12MP Adjustable focal | Need additional lens | 50
Camera | Raspberry pi cam module V2.1 | 8MP known FOV | fixed focal | 26
Stepper motor | Nema 17 10:1 | Torque of 3.5Nm Step angle of 0.18° | power supply of 8V and 35V | 47
Stepper motor | 28BYJ1 | 5V | Torque: 0.034Nm Less precise | 3

Table 1: Choice of components

For this project, we chose two Raspberry Pi 4, which will each have a camera plugged in. Both computer boards will be interconnected with a RJ-45 cable, and set up in a master-slave configuration. This allows the master to easily get the data from the slave, and then compute the stereovision.

We then chose an LCD touch screen to display an interactive user interface, which allows to set up, to start the scan and to save the 3D files.
We’re also taking two Raspberry Pi camera Modules V2.1, because they are affordable and have a sufficient resolution for our project.

The stepper motor 28BYJ-48 has a lot of steps, but the torque is very weak. Therefore, we chose the Nema 17, which has a much higher torque, and a stepping angle of 0.18°.

Finally, a 5mW laser, with a lens of divergence of minimum 60° in line will be able to cover the entire object.

3

### 2.1.2 Power consumption research

To power all the components, we would need two different voltage sources. The first one, in 5V, is used to power the raspberries, cameras, the display, the laser and the A4988 driver. This results in a consumption of 19.6W (Table 2).
On the other hand, the stepper motor, will be connected to the driver, and would need more voltage. We chose 12V as the second voltage, because it is easy to find an AC/DC converter that outputs those two voltages.

As we can see on Figure 3, the driver has 2 power connections : VDD in 5V and VMOT between (8-35V). VDD is used to power the logic components and drains up to 1.75W.
On the other hand, VMOT is used to power the stepper motor. The max current the driver can drain is 2A per coil, thus 4A in total. We are going to connect an power supply of 12V, resulting in 48W in power consumption in the worst case.
However, we will set the driver to drain a maximum of 1A per coil, resulting in a consumption, for our use case, of 24W.

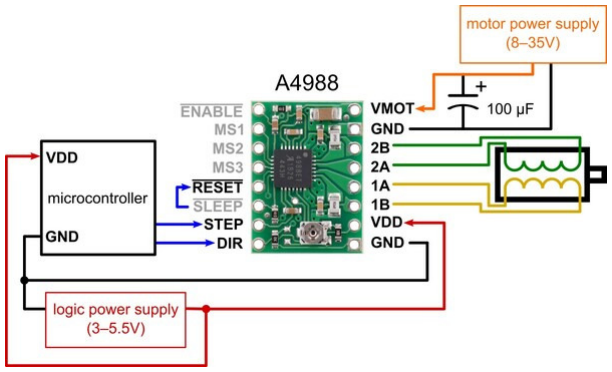
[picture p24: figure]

Figure 3: A4988 driver

Thanks to those results, we can choose the power supplies we would need for this project. We thus chose an AC/DC power supply with 2 outputs: one at 5V (5A) and the other at 12V (2A). This allows us to have a bit of headroom for the components connected in 5V, as well as the maximum power the driver would require (See BoM at Appendix C).

4

Component | Consumption
Raspberry pi 4 Raspberry pi cam v2 11” DSI display A4988 driver Red line | 2 * 5.5W 2* 1.4W 4W 1.75W 5mW
TOTAL (in 5V) | 19.6W
A4988 driver (max) Use case | 48W 24W
TOTAL (in 12V) | 24W

Table 2: Consumption

### 2.1.3 Sizing

Having chosen our components, we are able to dimension the prototype.

First, we use cameras whose maximum field of view is 62.2° (if positioned vertically). By trigonometry, we find that the camera must be at least 166mm from the object, if it is 200mm high.
To have a margin and ensure to take the whole object, the cameras will be placed at 200mm from the closest point of the object.

Then, the horizontal field of view being 48.8°, the cameras can be off-centered by a maximum of 90mm (beyond that, the red laser line is no longer in the field of view). The more they are off-centered, the more precise we can be to the calculation the depth of the points. The cameras will therefore be off centered by 75mm each.

The turntable having a diameter of 200mm, the cameras at 200mm from it and the Raspberry Pis and the screen behind the cameras, our prototype would measure about 500*200*150mm.

5

## 3 Measurement logic

### 3.1 Theory

In order to compute the depth, we are going to use the principle of triangulation. The depth of the point P is the distance z which we can express as z = f + d. We already know f from our camera’s specifications (the focal length) but we need to compute the distance d.
In order to do that, we will use the angle θl and θr. Indeed, as we know the distance b we will be able (thanks to the tangent of the angles θl and θr) to find the distance
d. We now need to find the angles θl and θr. To find them we use the field of vision of the camera.

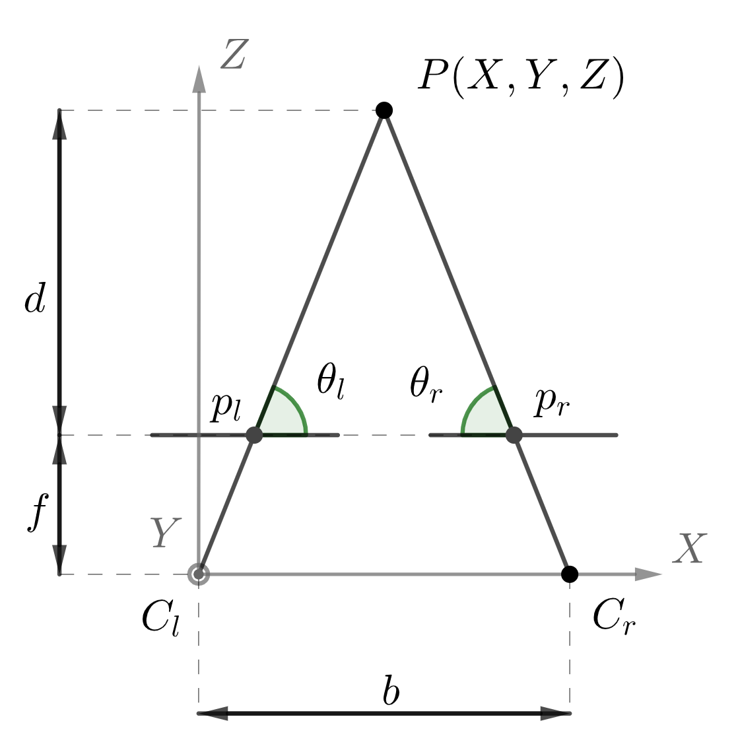
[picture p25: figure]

Figure 4: Principle of triangulation

6

Let’s define dim as the distance f, expressed in pixels. If our frame is of size (Wframe, Hframe) where Wframe and Hframe are given in pixels, and if we define ϕ as being the camera’s field of view, we can say that ϕ1 = ϕ2 =

ϕ
2

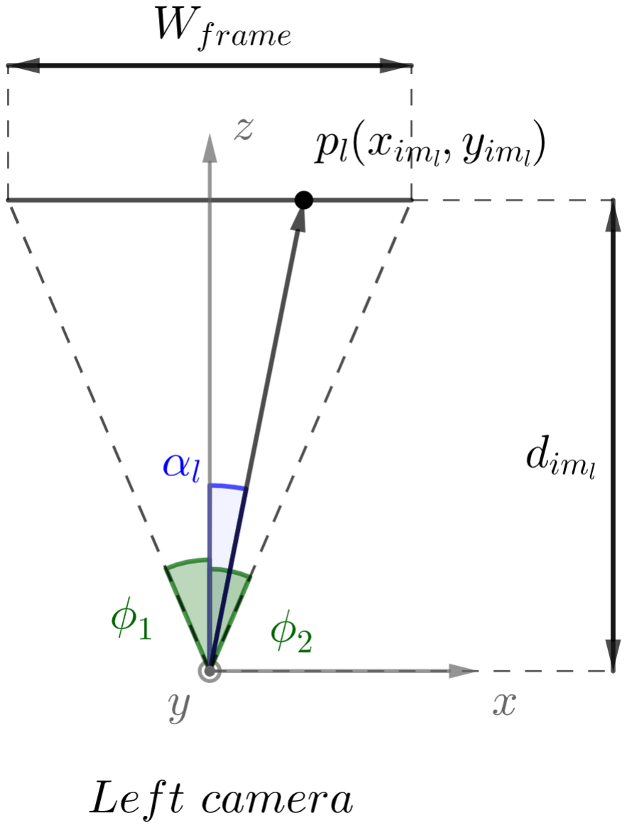
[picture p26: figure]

Figure 5: Field of vision of the camera c1 (left one)

We can find the distance dim thanks to the following relation :

tan(ϕ2) =

Wframe
2
dim | ⇔ tan(ϕ2) = Wframe
2∗dim | ⇔ dim =

Wframe
2∗tan(ϕ2

Now that we know the distance dim we can compute the angle α for every point pim = (xim, yim). Indeed we can say that :

tan(α) = Wframe−xim
dim ⇔ α = atan(

Wframe−xim

dim

)

We can now find the angle angle θl and θr. If we define αl and αr as being α for the left and right cameras respectively, we can see that :

90 = αl + θl ⇔ θl = 90 − αl

90 = αr + θr ⇔ θr = 90 − αR

With the same method, we can find the angle θr. Now that we have θl and θr, we can compute the distance d. Looking at Figure 4, we can then say that:

b =

d
tan(θl) +

d
tan(θr) ⇔ b =

d∗θr+d∗θl
θl∗θr ⇔ b =

d∗(θl+θr)
θl∗θr ⇔ d =

b∗θl∗θr
θl+θr

Having found d, we can now compute z which is :

z = f + d ⇔ z = f +

b∗θl∗θr
θl+θr

7

By replacing θl and θr by their expressions with αl and αr we find :

z = f +

b∗(90−αl)∗(90−αr)
(90−αl)+(90−αr)

By replacing αl and αr by they expressions with the coordinates of the points piml =

(ximl
, yiml

) and pimr = (ximr
, yimr

) we can say :

z = f +

b∗(90−atan(

Wf rame−ximl

diml

)∗(90−atan(

Wf rame−ximr

dimr

)

(90−atan(

Wf rame−ximl

diml

)+(90−atan(

Wf rame−ximr

dimr

)

By applying the same method, we are able to compute the Y coordinates of the point, which is why it will not be shown here.

## 4 Resolution and error on depth estimation

### 4.1 Resolution

The output resolution of the scan can be seen as the number of points of the 3D object model. Thus, the resolution depends on the number of pixels we are able to compute for each step, as well as on the number of steps in a full scan rotation. We can calculate this as follows:

R = s ∗ (Wlaser ∗ Hlaser)

where

- R is the resolution, in number of points
- s is the number of steps in a full scan rotation
- Wlaser is the width of the laser line, in pixels
- Hlaser is the height of the laser line, in pixels

8

### 4.2 Error computation on depth estimation

To compute the error on the depth measurement we use the propagation of error method. We can say :

∆z = |

∂z
∂xl

| + ∆xl + |

∂z
∂xr

| + ∆xr

∆z = |

b∗d∗(tan⁻¹
(

Wf rame−xr

dim

)−90)²

(d

2+(Wf rame−xl)

2∗(−tan⁻¹(

Wf rame−xl

dim

)−tan⁻¹(

Wf rame−xr

dim

)+180)²

| + ∆xl+

b∗d∗(tan⁻¹
(

Wf rame−xl

dim

)−90)²

(d

2+(Wf rame−xr)

2∗(−tan⁻¹(

Wf rame−xr

dim

)−tan⁻¹(

Wf rame−xl

dim

)+180)²

| + ∆xr

The calculations for Y are similar, since the Y coordinates are computed in a similar fashion.

## 5 Post-processing

Once we have the world coordinates of each point, we need to bring them together in order to build a point cloud. We will subsequently convert this point cloud into a polygon mesh that can be used for 3D printing.

To build a point cloud, we need to go through all the shots resulting from a full rotation. Each shot around the object will produce an array of relevant pixels. We then have to process those pixels, and for each one of them, we need to calculate the corresponding point in the obj coordinate system, whose origin will be at the center of the turntable.

9

For a point P = (X, Y, Z), whose coordinates Y and Z have previously been evaluated thanks to stereovision, we have to establish its coordinates according to the obj space, whose origin is the center of turntable.
In order to compute the angular value of the polar coordinates, we need to know the number of preceding steps since the start of the rotation, as well as the angle covered by one step of the motor. We can define Ns as the number of steps performed by the motor since the start of the rotation, and ϕs as the angle covered by one step of the motor.

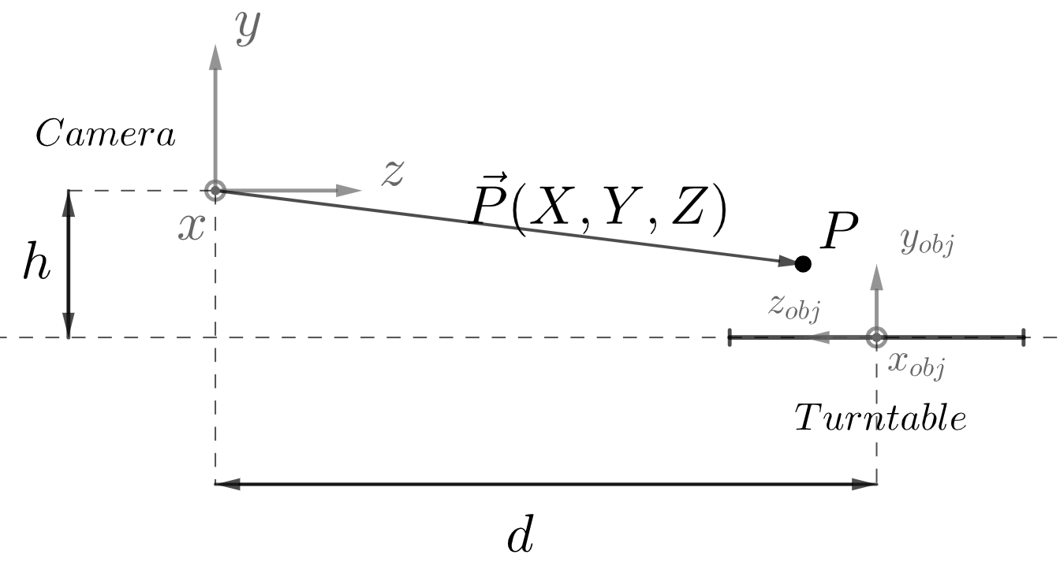
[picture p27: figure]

Figure 6: object coordinate change

We can then define P’, as the corresponding point to P, in the obj coordinate system:

P

′ = (r, yobj , θ)

where

- r = d − z
- yobj = h − Y
- θ = Ns ∗ ϕs

We can convert the polar coordinates to Cartesian coordinates as follows:

P

′
cart =

xobj | = r ∗ sin(θ)
yobj | = yobj
zobj | = r ∗ cos(θ)

10

Once we have the point cloud, we need to convert it into a polygon mesh. In order to achieve that, we will use the Python library PyMeshLab. (https://pymeshlab.readthedocs.io/en/latest/intro.html)
After that, the output should be able to be run into any file converter, so that the scanned object can be expressed into a wide range of 3D file types. The PyMeshLab library also provides several ways to enhance the object model, such as smoothing functions and other useful post-processing features, like the possibility to eliminate a portion of the data, in order to find a good compromise between quality and file size.

11

## References

[1] Aish Dubey. “Stereo vision—Facing the challengesand seeing the opportunities for ADAS applications”. In: (2020). url: https : / / www . ti . com / lit / wp / spry300a/spry300a.pdf (https://www.ti.com/lit/wp/spry300a/spry300a.pdf) (visited on 12/28/2021).
[2] Nicholas Ayache and C. Hansen. “Rectification of images for binocular and trinocular stereovision”. report. INRIA, June 1988. url: https://hal.inria.fr/inria-00075694 (https://hal.inria.fr/inria-00075694) (visited on 12/28/2021).
[3] Clayton Darwin. Distance (Angles+Triangulation) - OpenCV and Python3 Tutorial - Targeting Part 5. 2018. url: https://www.youtube.com/watch?v=sW4CVI51jDY (https://www.youtube.com/watch?v=sW4CVI51jDY) (visited on 12/26/2021).
[4] Cosmetic bag. DIY 3D Laser Scanner Using Arduino - Make: Make: DIY Projects and Ideas for Makers. Nov. 30, 2001. url: https://makezine.com/2013/05/24/new-project-diy-3d-laser-scanner-using-arduino/ (https://makezine.com/2013/05/24/new-project-diy-3d-laser-scanner-using-arduino/) (visited on 12/28/2021).
[5] DroneBot Workshop. Getting Started with LIDAR. 2018. url: https://www.youtube.com/watch?v=VhbFbxyOI1k (visited on 12/20/2021).
[6] dtrewren. Ciclop 3D Scanner (BQ & Horus). Instructables. url: https://www.instructables.com/Ciclop-3D-Scanner-BQ-Horus/ (visited on 12/29/2021).
[7] FU-Fighters. “Stereo vision with a single camera”. In: (2004). url: http://www.inf.fu-berlin.de/lehre/SS06/Robotik/stereo_vision_newest.pdf (visited on 12/20/2021).
[8] Enric Meinhardt Gabriele Facciolo Carlo de Franchis. “MGM: A Significantly More Global Matching for Stereovision”. In: (2015). url: http://dev.ipol.im/~facciolo/mgm/mgm.pdf (http://dev.ipol.im/~facciolo/mgm/mgm.pdf) (visited on 12/29/2021).
[9] In-Depth: Control 28BYJ-48 Stepper Motor with ULN2003 Driver & Arduino. Last Minute Engineers. Dec. 22, 2019. url: https://lastminuteengineers.com/28byj48-stepper-motor-arduino-tutorial/ (https://lastminuteengineers.com/28byj48-stepper-motor-arduino-tutorial/) (visited on 12/20/2021).
[10] Saad Merrouche et al. “Objective Image Quality Measures for Disparity Maps Evaluation”. In: Electronics 9.10 (Oct. 2020), p. 1625. url: https : / / www . mdpi.com/2079-9292/9/10/1625 (visited on 12/23/2021).
[11] Object Files (.obj). url: http://paulbourke.net/dataformats/obj/ (visited on 12/29/2021).
[12] Objet 3D (format de fichier). In: Wikip´edia. Page Version ID: 171551342. June 1, 2020. url: https://fr.wikipedia.org/w/index.php?title=Objet_3D_(format_de_fichier)&oldid=171551342 (https://fr.wikipedia.org/w/index.php?title=Objet_3D_(format_de_fichier)&oldid=171551342) (visited on 12/20/2021).
[13] OpenCV: Depth Map from Stereo Images. url: https://docs.opencv.org/4.x/dd/d53/tutorial_py_depthmap.html (https://docs.opencv.org/4.x/dd/d53/tutorial_py_depthmap.html) (visited on 12/29/2021).

12

[14] M. Pesce et al. “A Low-cost Multi Camera 3D Scanning System for Quality Measurement of Non-static Subjects”. In: Procedia CIRP. 3rd CIRP Global Web Conference - Production Engineering Research 28 (Jan. 1, 2015), pp. 88–
93. issn: 2212-8271. doi: 10 . 1016 / j . procir . 2015 . 04 . 015. (https://doi.org/10.1016/j.procir.2015.04.015) url: https : / / www . sciencedirect . com / science / article / pii / S2212827115002772 (https://www.sciencedirect.com/science/article/pii/S2212827115002772) (visited on 12/23/2021).
[15] Pololu - A4988 Stepper Motor Driver Carrier. url: https://www.pololu.com/product/1182 (https://www.pololu.com/product/1182) (visited on 12/26/2021).
[16] Stephen Se and Piotr Jasiobedzki. “Stereo-vision based 3D modeling and localization for unmanned vehicles”. In: International Journal of Intelligent Control and Systems 13 (Mar. 18, 2008). url: https : / / www . researchgate . net/publication/228618177_Stereo- vision_based_3D_modeling_and_ localization_for_unmanned_vehicles. (https://www.researchgate.net/publication/228618177_Stereo-vision_based_3D_modeling_and_localization_for_unmanned_vehicles)
[17] Super Make Something. DIY 3D Scanner (Arduino, 3D Printing, PCB Design, Stepper Motors, IR Sensing) - Super Make Something. Mar. 14, 2016. url: https://www.youtube.com/watch?v=-qeD2__yK4c (visited on 12/28/2021).
[18] The Coding Lib. Depth Estimation Using Stereo Vision - Computer Vision Project with OpenCV C++ Code. 2021. url: https : / / www . youtube . com / watch?v=snJVyfl9ZMg (https://www.youtube.com/watch?v=snJVyfl9ZMg) (visited on 12/20/2021).
[19] The FabScan Project - Media Computing Group - RWTH Aachen University. url: https://hci.rwth-aachen.de/fabscan (visited on 12/29/2021).
[20] What is a stereo vision camera? — Camera blog. url: https : / / www . e -consystems.com/blog/camera/camera-board/what-is-a-stereo-visioncamera/amp/ (https://www.e-consystems.com/blog/camera/camera-board/what-is-a-stereo-vision-camera/amp/) (visited on 12/20/2021).
[21] William Lovegrove. Single-camera stereo vision for obstacle detection in mobile robots. 2007. url: https://spie.org/news/0911-single-camera-stereovision- for- obstacle- detection- in- mobile- robots?SSO=1 (https://spie.org/news/0911-single-camera-stereo-vision-for-obstacle-detection-in-mobile-robots?SSO=1) (visited on 12/20/2021).
[22] Zhiyi Zhang Zhihua Lv. “Build 3D Scanner System based on Binocular Stereo Vision”. In: (2012). url: https://cie.nwsuaf.edu.cn/docs/20170614173931092961. pdf (https://cie.nwsuaf.edu.cn/docs/20170614173931092961.pdf) (visited on 12/20/2021).

13

# Appendices

## Appendix A Raci Matrix

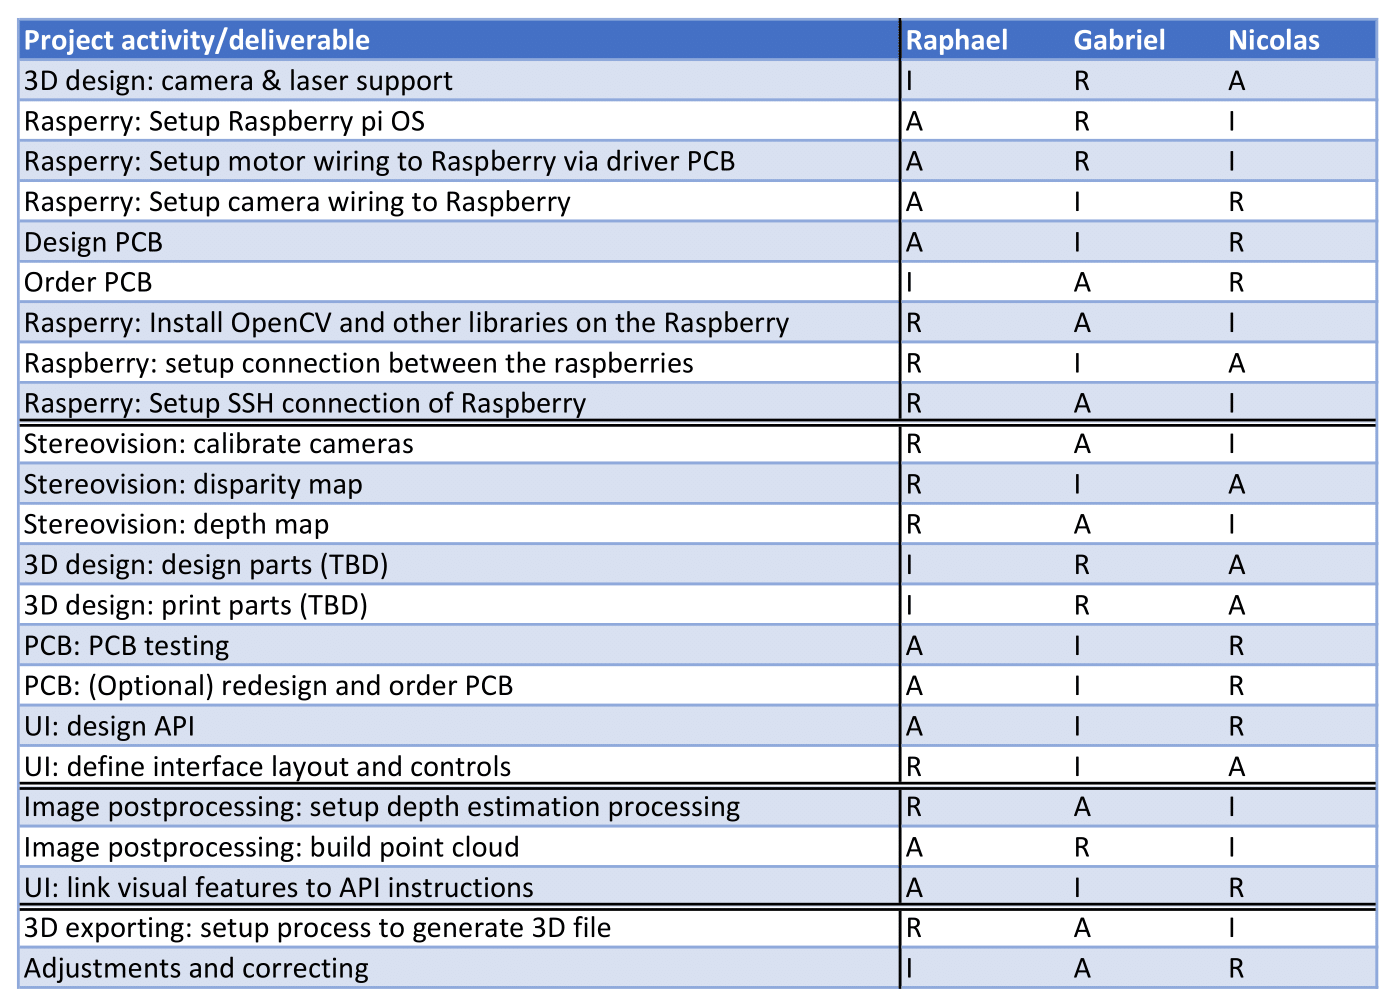
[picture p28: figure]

14

## Appendix B Gantt Diagram

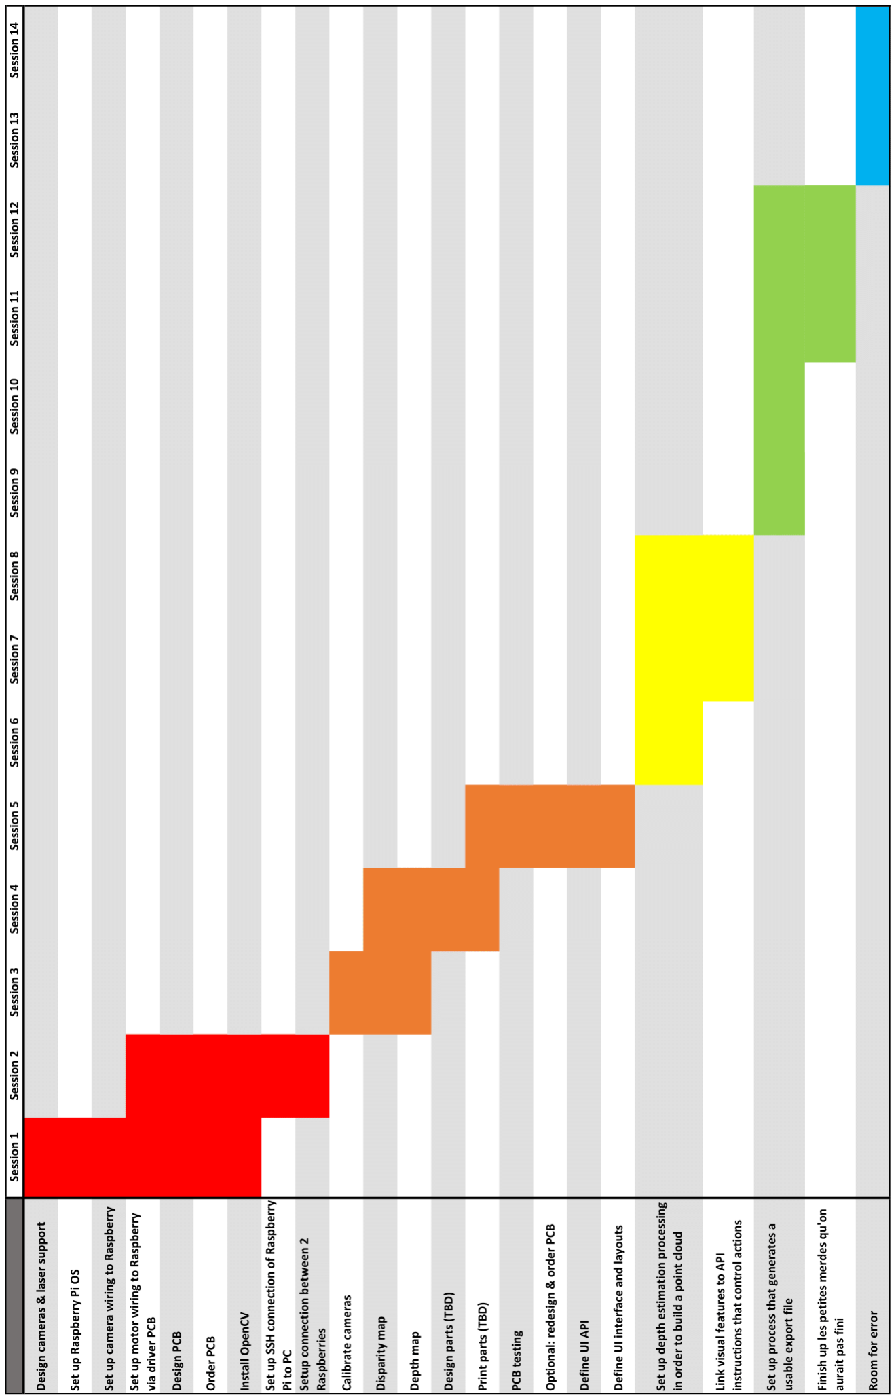
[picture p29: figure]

15

Appendix C | Bill of Materials
Name | Price [euro]
Raspberry Pi Camera Module V2.1 (https://be.farnell.com/fr-BE/raspberry-pi/rpi-noir-camera-board/raspberry-pi-noir-camera-board/dp/2510729) | 54
Stepper Nema 17 10:1 (https://www.omc-stepperonline.com/nema-17-stepper-motor-l39mm-gear-raio-101-high-precision-planetary-gearbox-17hs15-1684s-hg10.html) | 47
driver a4988 (https://www.omc-stepperonline.com/analog-stepper-driver/a4988-stepper-motor-driver-module-with-heat-sink-for-3d-printer-reprap-pack-of-5-pcs.html) | 7
Red line 5mW HLM1230 (https://www.amazon.fr/ARCELI-Module-lentille-Plastique-conducteur/dp/B07QDS8XZT/) | 9
Alimentation AC/DC 5V et 12V (https://be.farnell.com/fr-BE/mean-well/rpd-60a/alim-medicale-ac-dc-2-sorties/dp/2815574) | 27
Raspberry pi 4 * 2 | 104
Display 11” | 72
PCB | 30
TOTAL | 350

16

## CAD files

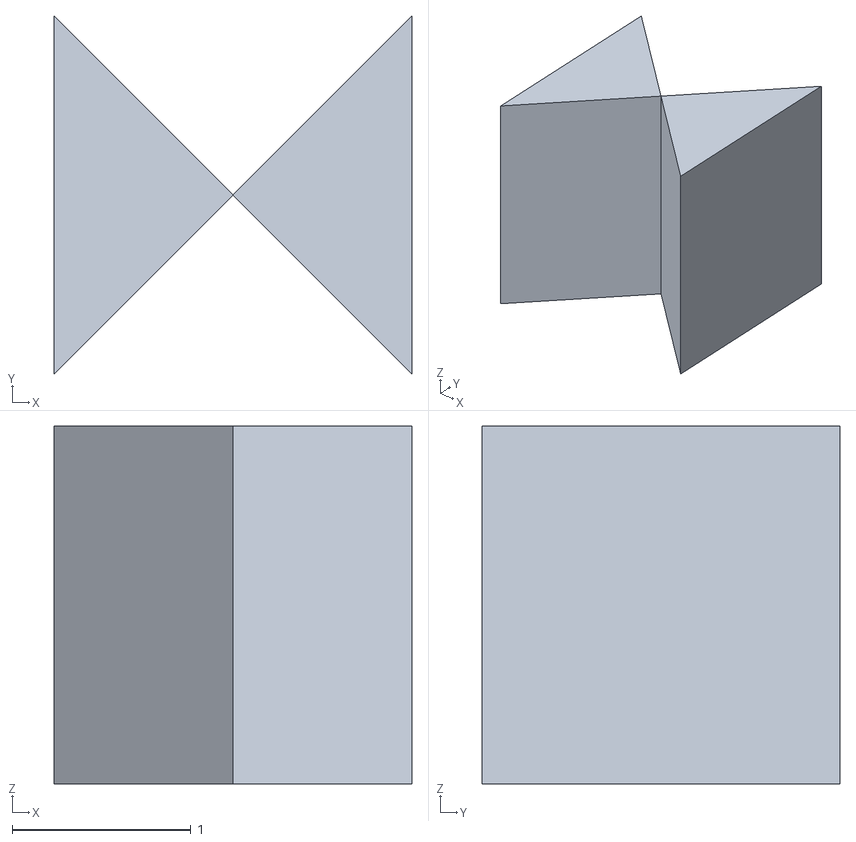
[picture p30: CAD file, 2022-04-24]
code/raspberry/post_processing/new_stl.stl
2.00 x 2.00 x 2.00

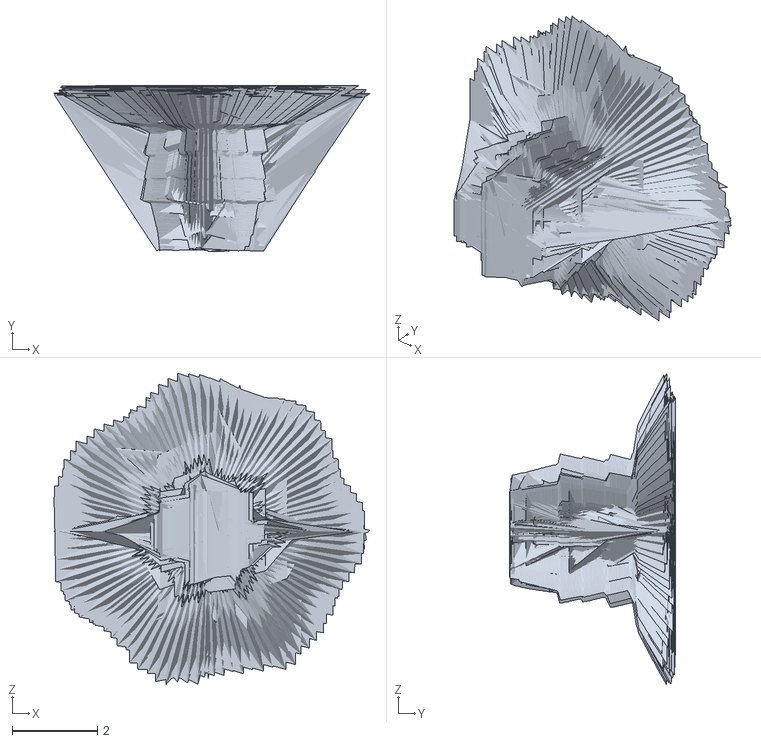
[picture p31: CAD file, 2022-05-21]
scans/scan_1/scan_1_by_SID.stl
7.43 x 3.91 x 7.32

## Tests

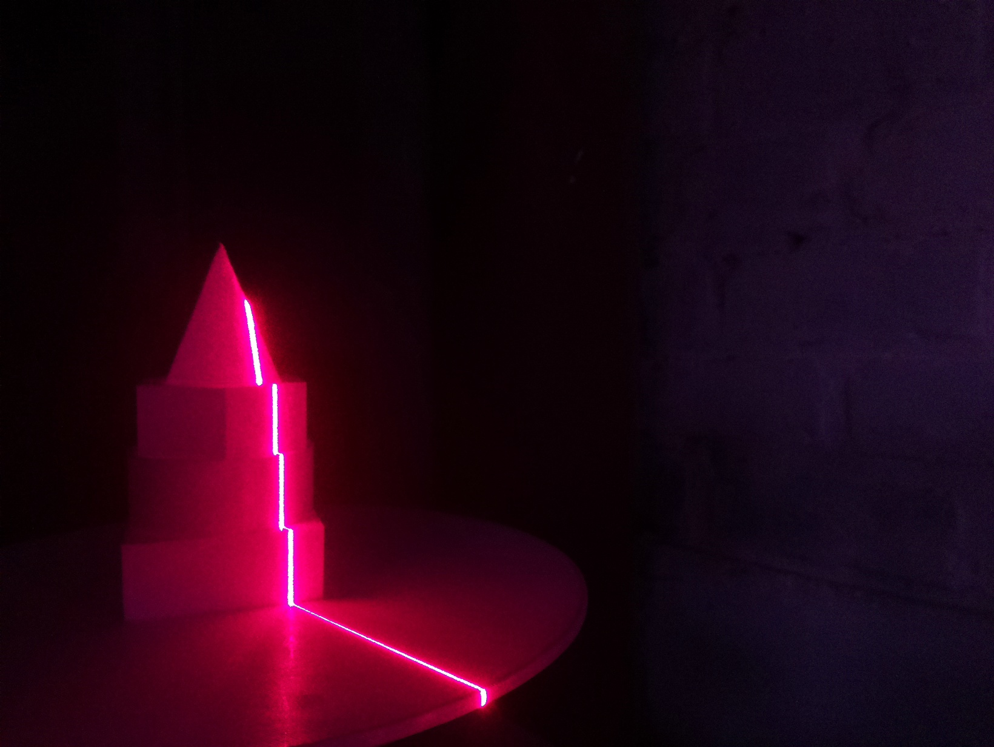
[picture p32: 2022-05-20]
code/raspberry/stereovision/test/scanLeft/test_L_82.jpg

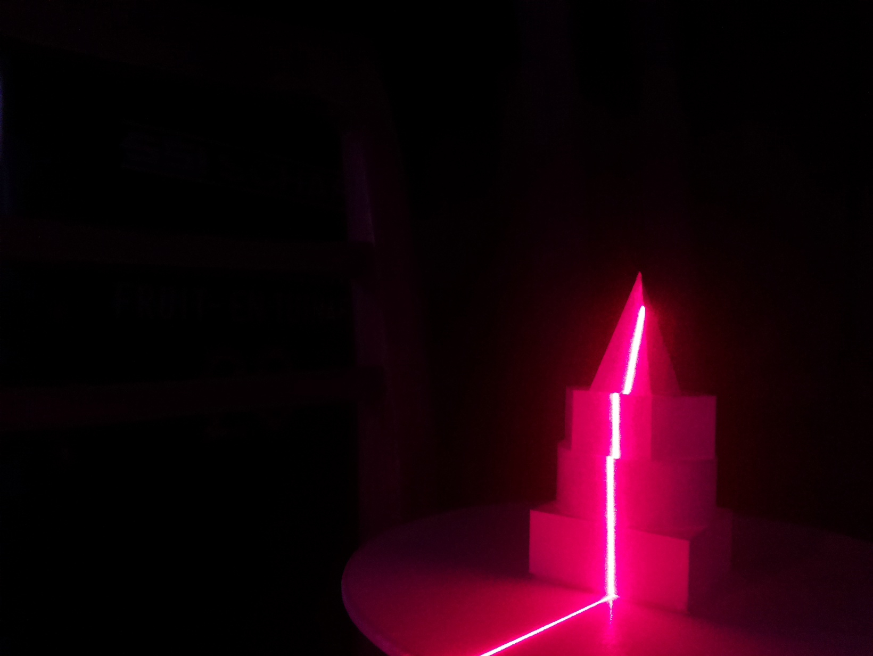
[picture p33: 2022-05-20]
code/raspberry/stereovision/test/scanRight/test_R_48.jpg

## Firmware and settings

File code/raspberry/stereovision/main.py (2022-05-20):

import calibration as cal
import image_processing as ip
import cv2
import numpy as np
from scan_processing import *
# from post_processing import *


mtx, dist, rvecs, tvecs, objp = cal.calibration()
F, camLeft, camRight, camWorldCenterLeft, camWorldCenterRight = cal.computeMatFund(mtx, dist, rvecs, tvecs)
print(camWorldCenterLeft, camWorldCenterRight)
cal.plotDotWorld(objp, camWorldCenterLeft, camWorldCenterRight)
# #print(camWorldCenterLeft, camWorldCenterRight)
computePointCloud4Scan("test")
# pre_revolution("test")

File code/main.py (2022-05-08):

from kivy.app import App
from kivy.uix.screenmanager import *
from kivy.core.window import Window

from screens.HomePageScreen import HomePageScreen 
from screens.RunScreen import  RunScreen
from screens.StorageScreen import StorageScreen
from screens.SettingsScreen import SettingsScreen

import raspberry.GPIO_setup as stp

class MainApp(App):
    
    def build(self):
        self.title = "SID alpha version 1.4"
        
        # Setup GPIO
        stp.gpioSetup()
        
        Window.fullscreen = False
        # build the screen manager
        sm = ScreenManager(transition=FadeTransition())

        sm.add_widget(HomePageScreen(name='Home'))
        sm.add_widget(SettingsScreen(name='Settings'))      
        sm.add_widget(RunScreen(name='Run'))
        sm.add_widget(StorageScreen(name='Storage'))
                
        return sm

if __name__ == '__main__':
    MainApp().run()

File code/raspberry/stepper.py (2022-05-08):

#######################################
# Copyright (c) 2021 Maker Portal LLC
# Author: Joshua Hrisko
#######################################
#
# NEMA 17 (17HS4023) Raspberry Pi Tests
# --- rotating the NEMA 17 to test
# --- wiring and motor functionality
#######################################

"""
source = https://makersportal.com/blog/raspberry-pi-stepper-motor-control-with-nema-17
TUTO = https://lastminuteengineers.com/a4988-stepper-motor-driver-arduino-tutorial/
library = https://github.com/gavinlyonsrepo/RpiMotorLib
"""


import RPi.GPIO as GPIO
from RpiMotorLib import RpiMotorLib
import time

################################
# RPi and Motor Pre-allocations
################################

# define GPIO pins
direction= 22   # Direction (DIR) GPIO Pin
step = 23       # Step GPIO Pin
EN_pin = 24     # enable pin (LOW to enable)

mymotortest = RpiMotorLib.A4988Nema(direction, step, (2,3,4), "A4988")
GPIO.setmode(GPIO.BCM)
GPIO.setup(EN_pin,GPIO.OUT) # set enable pin as output
GPIO.setup(EN_pin,GPIO.HIGH) # set enable signal to high, to lock the motor in place

'''
step size : 
Full = 1000 ; 0.36°
Half = 2000 ; 0.18°
1/4  = 4000 ; 0.09°
1/8 = 8000 ; 0.045°
'''

def makeStep(number_of_step, step_size, doEnd = True):
    #print(f"making {number_of_step} steps at {step_size} size")

    GPIO.output(EN_pin,GPIO.LOW)        # pull enable to low to enable motor
    mymotortest.motor_go(False,         # True=Clockwise, False=Counter-Clockwise
                        step_size ,     # Step type (Full,Half,1/4,1/8,1/16,1/32)
                        number_of_step, # number of steps
                        .1,            # step delay [sec]
                        False,          # True = print verbose output 
                        .05)            # initial delay [sec]
    if doEnd:
        GPIO.output(EN_pin,GPIO.HIGH)


def stopMotor():
    print("stop")
    mymotortest.motor_stop()
    GPIO.cleanup()


# TO RUN INDEPENDENTLY
#
#makeStep(4000,"1/4")
 

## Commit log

2022-02-21 added stepper script
2022-02-21 Add camera calibration
2022-02-22 moved pcb to another branch
    [BOM_PCB_PCB_sid_pm_2_2022-02-11.csv]
2022-02-22 Add calibration
2022-02-25 added laser
2022-02-26 linked laser script and cleaned stepper
2022-02-27 added fullscreen and exit button
2022-03-02 Add method to make step by step motor
2022-03-02 Uncomment code in the laser.py
2022-03-02 Add code of the stepper in the scan.py
2022-03-02 add motortest.py
2022-03-05 set laser as pwm
2022-03-05 Push from raspberry
2022-03-08 Add temporary scan for the new stepper
2022-03-08 Integrate the new motor
2022-03-09 implemented stepper
2022-03-19 stepper now working
2022-03-26 stepper runs from the interface
2022-03-30 creating stl file
    [new_stl_file.stl]
2022-04-07 mesh can be created
    [new_stl.stl, new_stl_file.stl]
2022-04-20 added centered mean point top to bottom
    [new_stl.stl]
2022-04-20 added sablier
    [new_stl.stl]
2022-04-24 cleaned + added calibration save
2022-05-07 Implement calibration pics capture
2022-05-08 Fix bux in scan.py
    [scan.py]
2022-05-08 Reset camera resolution
2022-05-08 projet de ses morts
2022-05-13 mieux si les images s'affichent
2022-05-21 final 3D STL
    [scan_1_by_SID.stl]
